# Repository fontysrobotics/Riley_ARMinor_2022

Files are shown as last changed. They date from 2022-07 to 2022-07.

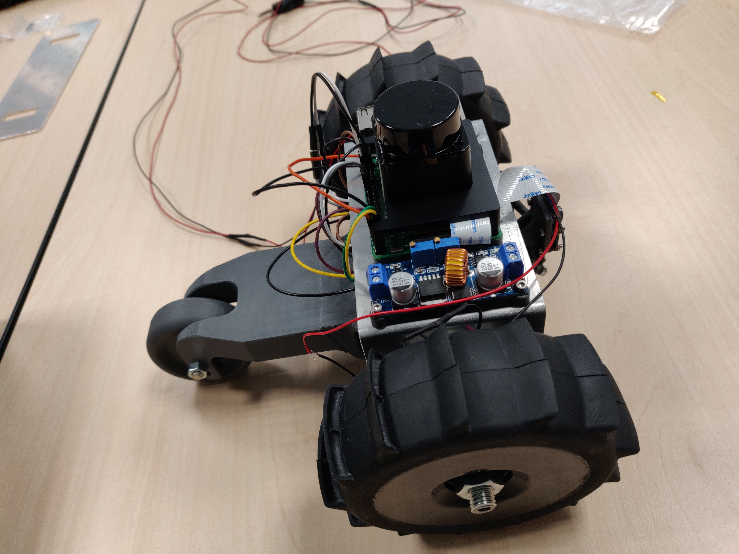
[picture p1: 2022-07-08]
docs/Environment_Preparations_RILey/pictures/Build-V0.1-Top.jpg

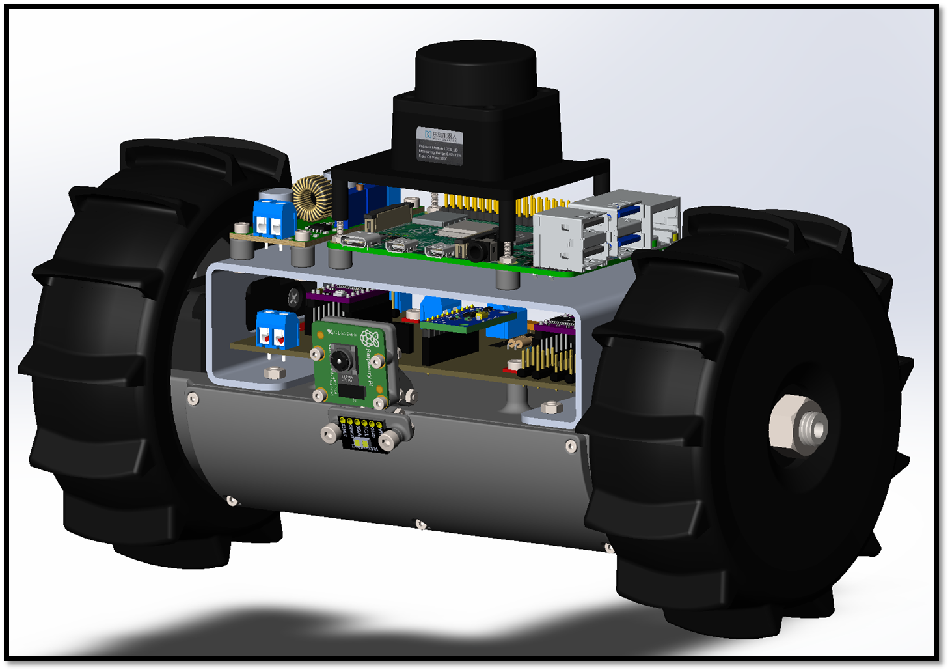
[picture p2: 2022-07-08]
docs/Environment_Preparations_RILey/pictures/LEGO_Assembly/Step17.png

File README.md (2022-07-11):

# Riley_ARMinor_2022
Remote indoor Inspection with Low-cost robots (RILey)
## Github file structure
- `docs` : in-development website containing documentation for the RILey robot, as well as pictures of the robot and meta information. Ideally could be run through Github Pages (can be setup in repository settings) but can also be built and run locally through VSCode.
- `documentation` : All documentation created during the project. This includes the initial project information, the plan of approach (before project requirements shifted drastically), datasheets for some of the components, the technical documentation for setting up many aspects of the robot and server systems, plus additional video material.
- `electrical` : Documentation related to the electrical design of the RILey robot, including version 1 and 2 of the PCB design, notes regarding problems encountered in the PCB design and explanations/schematics for the global electrical connections.
- `ros2` : Code files needed to run the robot (physical and simulation) through ROS2-foxy. More info included in technical document. Included are:
  - `riley_ws` : Main ROS workspace containing all the packages and launch files for both robot and server side.
  - `simulation` : ROS workspace used for simulating the robot in a virtual environment (Gazebo).
  - `yolov5` : Separate directory used to store the YOLOv5 object recognition model.
- `solidworks` : Solidworks CAD files making up version 1 and 2 of the RILey robot, including imported assets. Additional folders for STL/DXF component exports also available, though not needed for the CAD assemblies.

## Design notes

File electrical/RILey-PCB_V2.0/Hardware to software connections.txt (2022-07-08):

Physical pin:	GPIO pin:	Connection:
01:			None	:	3V3,	used by TOF
02:			None	:	5V,	used to power the Raspberry Pi 4b
03:			2	:	SDA,	used for I2C to sensors
04:			None	:	5V,	used to power the Raspberry Pi 4b
05:			3	:	SCL,	used for I2C to sensors
06:			None	:	GND,	used for power
07:			4	:	NC,	spare available at front pins labeled 14
08:			14	:	TX,	spare available at front pins labeled 15	
09:			None	:	GND,	used for power	
10:			15	:	RX,	used for receiving lidar information	
11:			17	:	lidar 'pwm' pin, used for rotation speed
12:			18	:	lidar enable pin, used to turn on the lidar
13:			27	:	NC,	spare available at front pins labeled 13
14:			None	:	GND,	used for power
15:			22	:	stepper motor mode0
16:			23	:	stepper motor mode1
17:			None	:	3V3,	used by TOF
18:			24	:	stepper motor mode2
19:			10	:	NC,	spare available at front pins labeled 12
20:			None	:	GND,	used for power
21:			9	:	NC,	spare available at front pins labeled 11
22:			25	:	NC,	spare available at front pins labeled 10
23:			11	:	NC,	spare available at front pins labeled 9
24:			8	:	NC,	spare available at front pins labeled 8
25:			None	:	GND,	used for power
26:			7	:	NC,	spare available at front pins labeled 7
27:			0	:	NC,	spare available at front pins labeled 6
28:			1	:	NC,	spare available at front pins labeled 5
29:			5	:	stepper motors disable
30:			None	:	GND,	used for power
31:			6	:	stepper motor 1 direction
32:			12	:	stepper motor 1 step
33:			13	:	stepper motor 2 step
34:			None	:	GND,	used for power
35:			19	:	NC,	spare available at front pins labeled 4
36:			16	:	NC,	spare available at front pins labeled 3
37:			26	:	stepper motor 2 direction
38:			20	:	NC,	spare available at front pins labeled 2
39:			None	:	GND,	used for power
40:			21	:	NC,	spare available at front pins labeled 1

Legend:
3V3:	3.3 Volt
5V:	5 Volt
SDA:	one of the I2C lines
SCL:	one of the I2C lines
GND:	ground
NC:	Not Connected / not used / available
TX:	uart transmit
RX:	uart receive

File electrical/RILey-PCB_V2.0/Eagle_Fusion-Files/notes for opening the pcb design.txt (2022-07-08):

If you want to open the "RILey-PCB_V2.0_v99.f3z" file, you have to open fusion (360) and make a workspace, and upload this file.
Then it downloads all the files that have been made before.

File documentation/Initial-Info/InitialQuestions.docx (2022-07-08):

1. Main use cases with examples. What should be prioritized?
- As many as possible, priority is our choice
- Collapsed area, eventually finding humans. (search and rescue)
2. Are CAD files and software files available for the prototype and completed robot?
- Company question.
3. Hardware datasheet with specifications for the sensors, robot manual and other documentation?
- Should be.
4. Does it need to go outdoors?
- No
5. Does it need to climb ramps or do other non-2D movements?
- No 3D needed.
6. Can we adjust existing parts of the robot or only add new ones?
- If needed you can add, if justified. (modifying not sure yet)
7. What’s the budget? Define Low-cost.
- Below €10k, currently the robot is €3k.
- Everything is discussed with Sjriek. (€1k generic)
8. Upside down movement, is it possible/defined as a use case?
- Not a question, NO.
9. What should be inspected/detected (things)?
- As many as possible, at least 3 (must), up to 10 (should), more (could)
10. When do we get the physical robot?
11. What comm protocol does the robot use to communicate with the server?
- Wifi for now, other as a should
12. What should be the server specifications?
- For now your laptop.
13. Should manual override still be available?
- Yes
14. What kind of alerts should the robot send to operators?
- Company question
15. Are we allowed to modify the given physical robot?
- Look above
16. Should the robot try to “save itself”? I.e., return to exit in case of low battery.
- YES

Multiple robots working together: Must? (should) (cool, really nice)

Other ideas:

- Add LiDAR (think 360 vs fixed FoV, Flash vs line scan)

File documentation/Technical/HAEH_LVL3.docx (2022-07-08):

Adaptive Robotics minor

Hardware Abstraction & Embedded Systems

28-6-2022

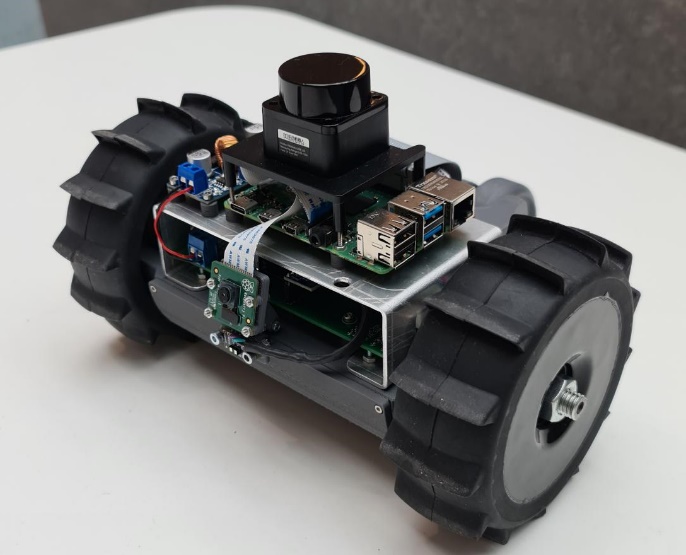
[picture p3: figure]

Name: Student number:

Toby van Dueren den Hollander 3679438

Quinvey Etienne 3566293

# Introduction

The Riley is a collaboration project between TMC and Fontys. TMC has approached Fontys with the goal of making their robot platform smarter with the use of additional sensor and logic. These improvements should make it possible to do autonomous reconnaissance of a building.

Because of IP related problems the platform itself could not be obtained from TMC. Therefore a mockup of the platform was made during the first months of the project. The dimensions and general shape of the mockup was modeled in a way to represent the original robot as accurate as possible.

In order to aid human and autonomous operations a few extra functions have to be added to improve control of the RILey robot platform.

# Problem Definition

During operation of the platform a few problems came up regarding movement and perception of the robot in its environment.

### Flipping

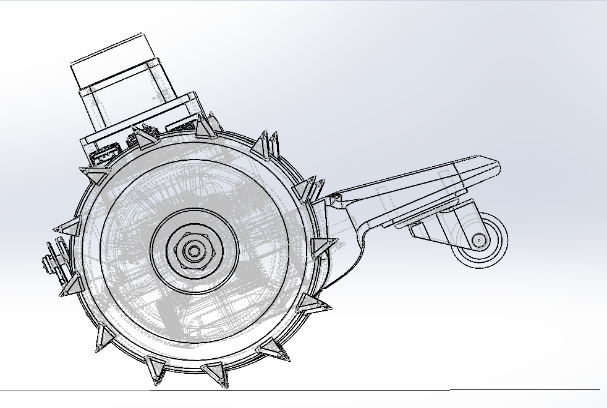
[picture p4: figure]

The first problem regards accelerating in backwards direction. The robot was initially designed to only drive forward. Accelerating backwards too quickly will result in a rotation flipping the robot as seen in the image below.

ω_rot

A_accel

Figure 1 Robot rotating

### colliding

Secondly, the lidar is able to visualize the surrounding of the robot. However, when objects are below the height of the lidar, the robot will not be able to detect the obstruction. This results in the robot bumping into smaller objects as seen below.

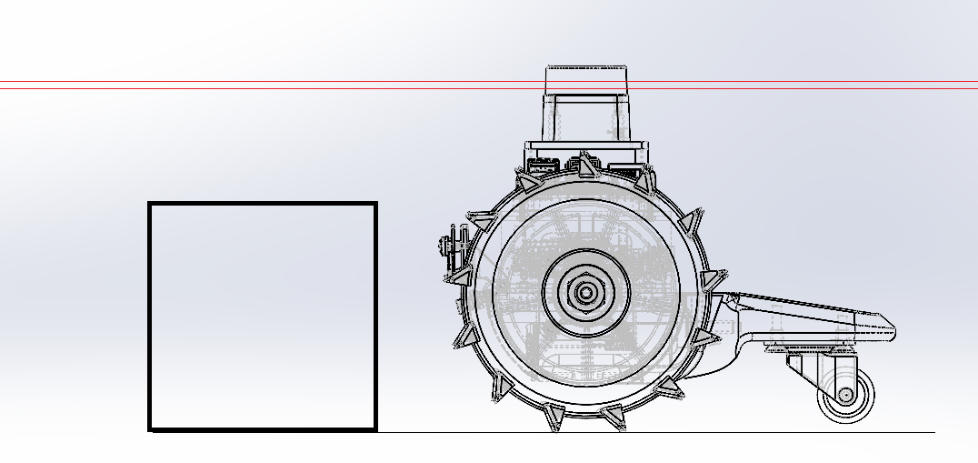
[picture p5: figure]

Figure 2 Robot just before hitting object

### Falling

Lastly the robot is not able to detect the presence of gaps, holes or other height differences in terrain. This can result in the robot falling of surfaces such as stairs.

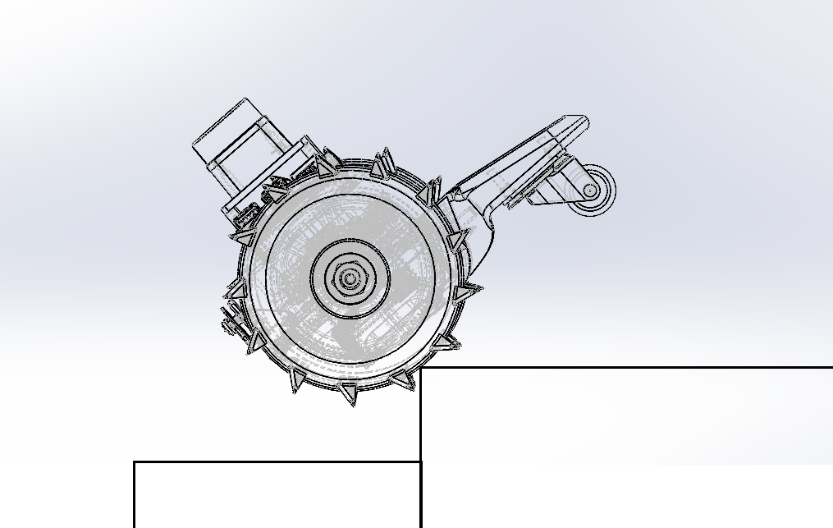
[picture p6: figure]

Figure 3 Robot falling of edge

# Solution of the problems

To provide a solution for the problems described above additional sensors are added to the robot. These include the MPU9250 and the VL53L1X. The MPU9250 contains a 3 axis gyroscope. This gyroscope can sense changes in the angular orientation of the robot. This can help preventing the robot from flipping. The VL53L1X Time of Flight sensor can measure distance by using infrared light. This sensor was used to prevent the robot hitting objects or driving into gaps.

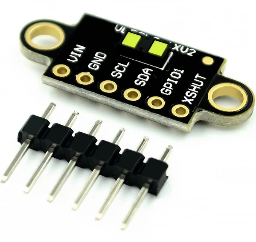
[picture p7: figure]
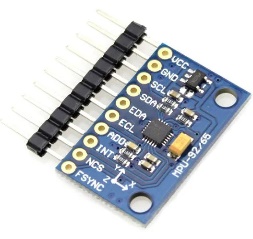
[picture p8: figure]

Figure 4 MPU9250 (left) and VL53L1X (right)

To prevent the robot from hitting a object the measured distance from the sensor cannot be less then a predefined threshold value. If this threshold value is reached, this means that there is a object on the robots track.

If the distance exceeds the threshold value corresponding to a gap value the robot will detect a gap.

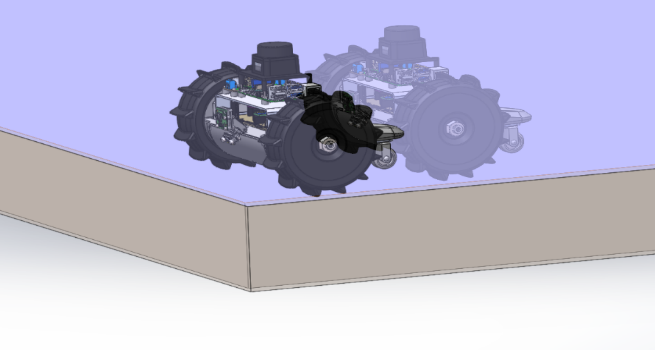
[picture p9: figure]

In both cases the robot should reverse so that it can easily turn away without hitting the object, or falling into the gap. The descision making is done on the raspberry pi itself. It overwrites input from both the user and/of the autonomous control.

Figure 5 Robot detecting gap

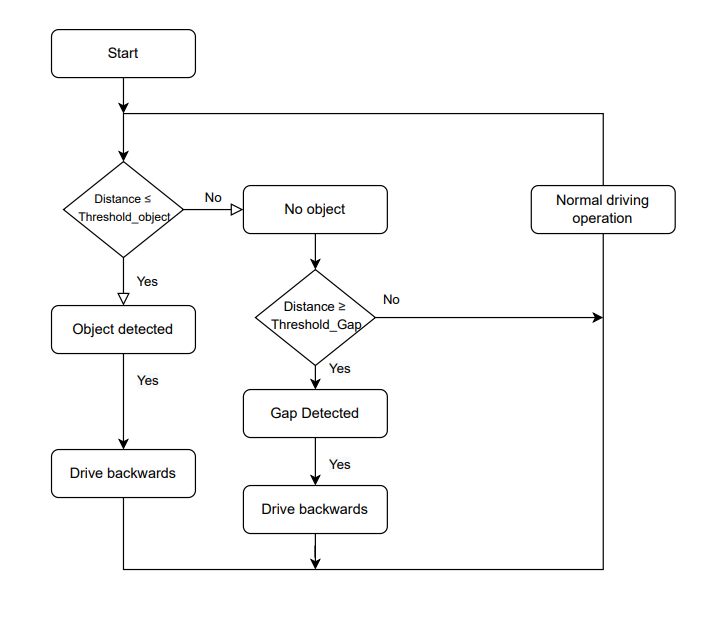
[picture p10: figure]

Figure 6 Logic illustrated in a flow chart

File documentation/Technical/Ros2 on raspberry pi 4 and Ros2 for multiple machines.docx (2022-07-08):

# Install ROS2 Foxy on Raspberry Pi 4

In this tutorial you will learn how to install ROS2 Foxy Fitzroy on Raspberry Pi 4.

ROS2 is a great framework/middleware for robotics applications. With a Raspberry Pi board you can go much further, and embed a complete ROS2 application inside a small robot.

For example, if you want to build a mobile base with wheels and a camera, well a Raspberry Pi 4 will be perfect for that. You can then create a network of robots all connected together.

## Which Raspberry Pi 4 version for ROS2 (RAM specs)

As you may know, the Raspberry Pi 4 board comes with different possible hardware configurations. You can choose between 2, 4 or even 8GB of RAM (previously also 1GB but discontinued).

If you currently have the 1GB version: 1 GB for Ubuntu Server + ROS2 is enough, but you’ll probably be limited in the future if you try to start more than a few nodes and launch files. If you want to avoid doing some optimization because of the RAM, I suggest you go with the 2GB (or more) version of the board.

After 2GB, then it’s quite simple: more RAM means more expensive. For starting and prototyping with ROS2, 2GB should be enough.

And one thing to keep in mind when using ROS2 on a Raspberry Pi: the Pi is certainly not as powerful as your computer/laptop, so you won’t be able to do 100% of what you do in your laptop, and some heavy features might run slower.

## Prerequisites: install Ubuntu Server 20.04

First you will need to install Ubuntu Server 20.04 on your Raspberry Pi 4 (https://roboticsbackend.com/install-ubuntu-on-raspberry-pi-without-monitor/).

We’ll use Ubuntu Server here because it’s probably the best suited OS for ROS2 on Raspberry Pi. ROS2 is really easy to install and works well on Ubuntu. For this tutorial you won’t need a desktop with Ubuntu on your Pi.

Also, as we’ll install ROS2 Foxy, make sure you have the version 20.04 for Ubuntu, since each version of ROS2 is only compatible with one Ubuntu version.

Once everything is setup and you have an Internet connection + ssh access to your Pi, you can start installing ROS2.

## Install ROS2 on Ubuntu on Raspberry Pi 4

Make sure to execute the commands in the order.

### Setup locale

sudo apt update && sudo apt install locales

sudo locale-gen en_US en_US.UTF-8

sudo update-locale LC_ALL=en_US.UTF-8 LANG=en_US.UTF-8

export LANG=en_US.UTF-8

### Setup sources

sudo apt update && sudo apt install curl gnupg2 lsb-release

sudo curl -sSL https://raw.githubusercontent.com/ros/rosdistro/master/ros.key -o /usr/share/keyrings/ros-archive-keyring.gpg

echo "deb [arch=$(dpkg --print-architecture) signed-by=/usr/share/keyrings/ros-archive-keyring.gpg] http://packages.ros.org/ros2/ubuntu $(source /etc/os-release && echo $UBUNTU_CODENAME) main" | sudo tee /etc/apt/sources.list.d/ros2.list > /dev/null

### Install ROS2 core packages

Now that you have added the ROS2 repository to your sources list, update.

sudo apt update

And now you can install ROS2.

Important: here we won’t install ros-foxy-desktop, we’ll install ros-foxy-ros-base, which contains no GUI tools, just the bare minimum you need to write and execute your ROS2 programs.

sudo apt install ros-foxy-ros-base

The ros-foxy-ros-base package is in fact a collection of many other packages, so the list of stuff to install will be pretty big. This step may take a few minutes to complete.

### Install colcon (build tool)

After you’ll write some ROS2 code into your own packages, you’ll need to build those packages.

ROS2 uses colcon as a build tool (and ament as the build system). When you only install the ROS2 core packages, colcon is not here, so install it manually.

sudo apt install python3-colcon-common-extensions

### Auto-completion for ROS2 command line tools

ROS2 comes with a lot of useful command line tools, and if you want to be able to use auto-completion for those tools, you’ll need to install The argcomplete Python module. First make sure you have pip3 installed.

sudo apt install python3-pip

pip3 install argcomplete

## Setup your environment for ROS2

Great, ROS2 Foxy is now installed on your Raspberry Pi 4 with Ubuntu Server 20.04!

Now, in order to actually use ROS2, you’ll need to setup your environment every time you open a new session (terminal). To source your ROS2 installation in your environment, run

source /opt/ros/foxy/setup.bash

And because it won’t be that practical to do this for every new session you open, add this line to your bashrc.

echo "source /opt/ros/foxy/setup.bash" >> ~/.bashrc

So, from now on, every time you open a terminal, your bashrc will be executed and your environment will be ready for ROS2.

## A few tips on how to best use ROS2 on Raspberry Pi

As you saw during the installation, we didn’t install any GUI tool, just the minimum to get things running.

If you need to use some visualization tools, such as Rviz or Gazebo, or if you need to do some heavy processing, then you might use a multi-machine setup with your Pi (or multiple Pis) and a more powerful computer/laptop. It’s very easy to make multiple machines communicate between each other with ROS2. You can run the programs that control hardware on your Raspberry Pi, and then exchange data – through ROS2 communication features – with your laptop, which will handle any GUI or heavy processing tasks.

Also, as you’ve only installed the core base, you might sometimes have to install additional packages.

To install a new ROS2 package, it’s quite easy: the name of the package will be “ros-distribution-package-name”. So if you want to install, on ROS2 Foxy, the example-interfaces package (which contains message and service definitions you can use when you get started with ROS2), you will run

sudo apt install ros-foxy-example-interfaces

# ROS2 Multiple Machines Tutorial (including Raspberry Pi)

In this tutorial you will learn how to run ROS2 on multiple machines, including a Raspberry Pi 4 board. As you’ll see, things will be quite easy and there is almost no configuration to do.

If you’re using a Raspberry Pi with ROS2 as one of the machines, make sure you have correctly installed ROS2 on your Pi (https://roboticsbackend.com/install-ros2-on-raspberry-pi/). Then, as you’ll see, no extra setup is required.

For this tutorial I will personally use a laptop running Ubuntu on a virtual machine (with a bridged adapter), and a Raspberry Pi with ROS2 on Ubuntu Server.

## Network configuration for ROS2 multi-machines

Before starting, obviously make sure you have installed ROS2 on each machine, preferably the same distribution.

Then, make sure you don’t have a firewall blocking your communications on the network. If you have a firewall, allow UDP multicasting, or disable the firewall at least during your first tests.

Connect all your machines in the same network. This is very important, otherwise they simply won’t be able to find each other.

Now, you can easily check if the machines can reach out to each other.

First, get the IP address of each machine inside the network by running

hostname -I

Example:

- Machine 1:
- hostname -I
- returns 192.168.43.138 172.17.0.1
- Machine 2:
- hostname -I
- returns 192.168.43.56

You may have multiple IP addresses on each machine, depending on what you’ve previously configured (ex: on Machine 1 I have Docker, this is why you see 172.17.0.1). Just find the IP addresses that are on the same network, here those who start with 192.168.43.xx.

If you can ping the machines from each other then the network configuration is done.

Machine 1:

$ ping 192.168.43.56

PING 192.168.43.56 (192.168.43.56) 56(84) bytes of data.

64 bytes from 192.168.43.56: icmp_seq=1 ttl=64 time=128 ms

64 bytes from 192.168.43.56: icmp_seq=2 ttl=64 time=136 ms

^C

Machine 2:

$ ping 192.168.43.138

PING 192.168.43.138 (192.168.43.138) 56(84) bytes of data.

64 bytes from 192.168.43.138: icmp_seq=1 ttl=64 time=8.75 ms

64 bytes from 192.168.43.138: icmp_seq=2 ttl=64 time=132 ms

^C

## Run ROS2 on 2 machines

Now it’s very simple. All you have to do is to start some nodes in Machine 1, some other nodes in Machine 2, and they will all be able to communicate through topics, services and actions. Just like they were all in the same machine.

Machine 1:

$ source /opt/ros/your_ros2_distribution/setup.bash # You can put that line into your ~/.bashrc

$ ros2 run demo_nodes_cpp talker

Machine 2:

$ source /opt/ros/your_ros2_distribution/setup.bash # You can put that line into your ~/.bashrc

$ ros2 run demo_nodes_cpp listener

And you should see logs on both machines!

If you want to communicate with a third/fourth/… machine, simply follow the network configuration steps again, and you’ll be all set.

## Use ROS_DOMAIN_ID to run multiple (separate) ROS2 applications on the same network

So, after you’ve configured the machines to be in the same network, they are all part of the same ROS2 application. This can be a problem: what if you want to run 2 different ROS2 applications on the same network and on multiple machines? Here you might want to completely separate the applications from each other.

Well, that’s possible, you just need to set one environment variable before you start your nodes.

Before you start any node in one session (= one terminal), you need to export a new environment variable, named ROS_DOMAIN_ID, using a number for the value (preferably a low number, between 1 and 232). Then, only the nodes started in sessions with the same ROS_DOMAIN_ID will be able to communicate with each other.

Example:

Machine 1 – session (terminal) A:

$ export ROS_DOMAIN_ID=5

$ source /opt/ros/your_ros2_distribution/setup.bash

$ ros2 run demo_nodes_cpp talker

Machine 2 – session (terminal) B:

$ export ROS_DOMAIN_ID=5

$ source /opt/ros/your_ros2_distribution/setup.bash

$ ros2 run demo_nodes_cpp listener

Try to set a different ROS_DOMAIN_ID (or don’t set one at all) on Machine 2 – session B, and you’ll see that the communication won’t work.

Now, you can have any number of configuration:

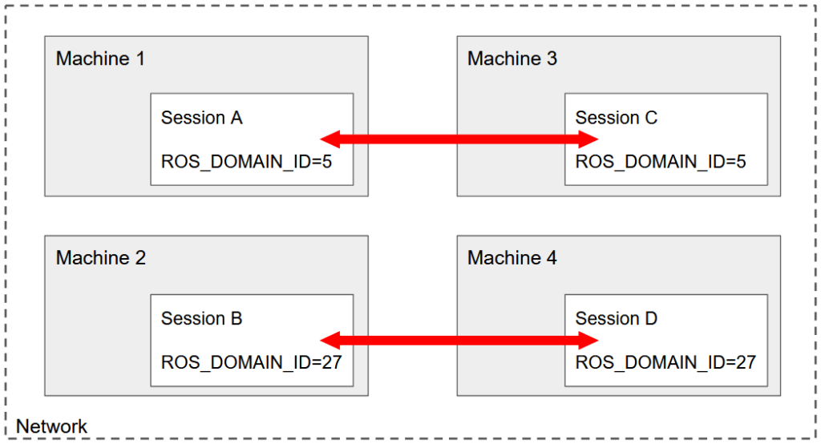
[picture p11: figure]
ROS2 Multiple Machines - Example with 4 Machines

Here you have 4 different machines, each starting one session. This is a classic example of what you can setup in real life.

In the future, make sure you don’t forget the ROS_DOMAIN_ID. If you know that all your sessions inside one machine will be used for the same application, you can add

export ROS_DOMAIN_ID=xx

to your ~/.bashrc.

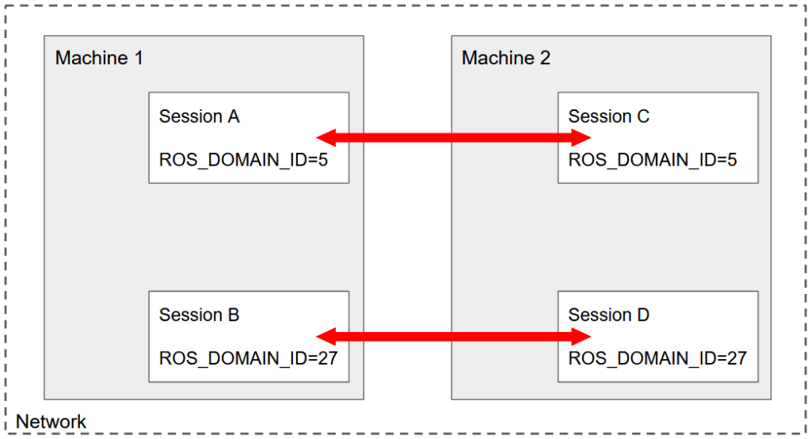
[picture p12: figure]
ROS2 Multiple Machines - Example with 2 Machines and 4 Sessions

But… You can also run multiple ROS2 applications on just 2 machines! What’s important is to understand that the ROS_DOMAIN_ID configuration is working at the session level, not the machine level – because it’s an environment variable.

## ROS2 multi-machine with Raspberry Pi

Running ROS2 across multiple machines is especially useful when you have a robot powered by a Raspberry Pi board, or any kind of embedded computer suitable for ROS2 (ex: Jetson Nano). Setting up your Pi for multi-machines communication is the same as setting up any other computer/laptop.

So, here is just an additional tip/best practice to keep in mind whenever you need to work with a robot powered by a Raspberry Pi.

If you want to make some experiments, or work with the robot simulation on the side, or do some heavy computing, etc., here is what you can do:

On your Raspberry Pi, just install the core packages, and run only the core nodes of your applications, which are responsible for talking to the hardware. Then, on your other (remote) computer, start any simulation tool such as RViz, Gazebo. Start your heavy nodes such as motion planning, etc.

This is a great way to minimize the CPU and RAM use on your Pi, and also to speed up your development time.

All in all, multiple machine communication is a really powerful ROS2 functionality. With ROS2 you can build a complete distributed system, not only on the software side, but also on the hardware side.

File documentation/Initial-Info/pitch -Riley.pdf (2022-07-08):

## Remote Inspection with Low-cost robots

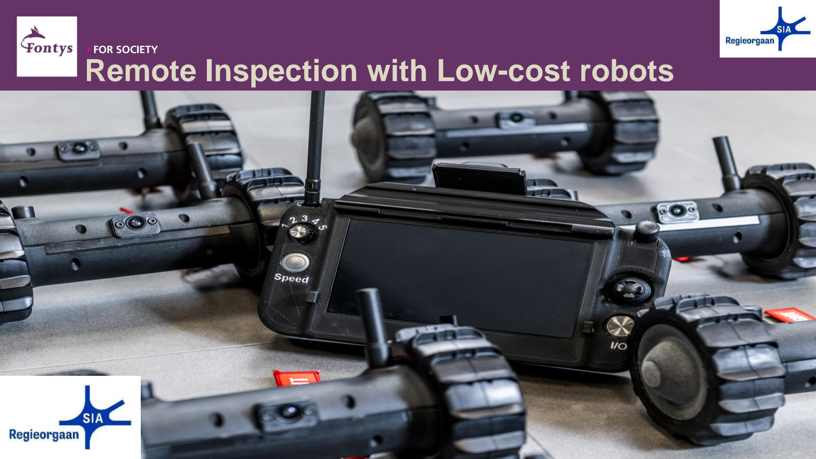
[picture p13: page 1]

- RILey is a project where we would like to accomplish technical challenges related to enable autonomous inspection for low cost robots in indoor our outdoor environments.
- In this project we would like to implement, improve and validate autonomous remote control of the SITA robot, that is provided by SITA Robotics, TMC and Avular are technology partners in this project. The project is funded by SIA.

# General Project Focus

Can we use the existing low-cost SITA robot, which is intended for remote-controlled reconnaissance, for autonomous inspection without substantially modifying

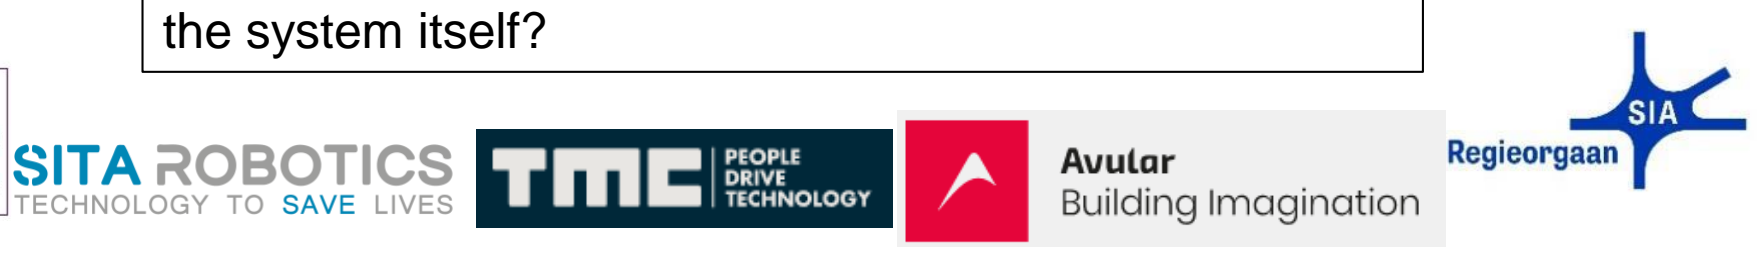
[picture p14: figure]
the system itself?

# Impression SITA robot

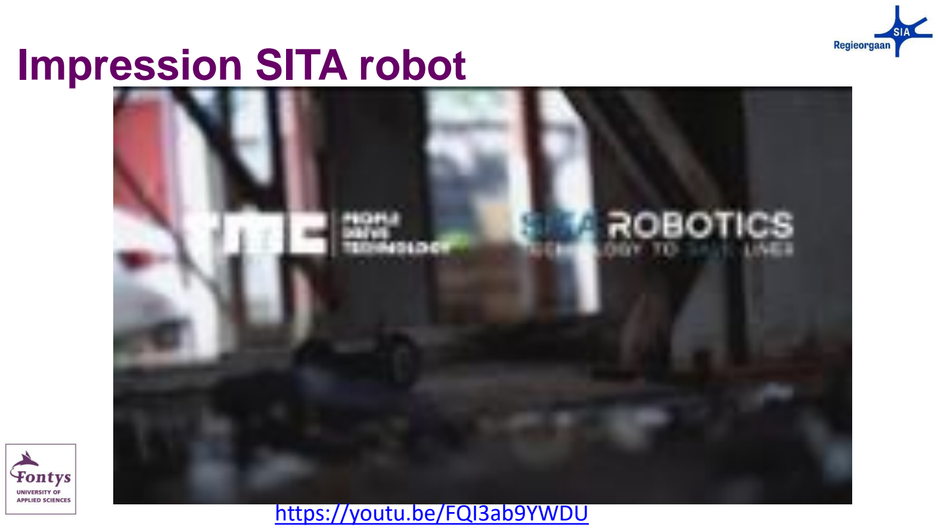
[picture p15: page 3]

https://youtu.be/FQI3ab9YWDU

## - How can you efficiently and autonomously scan a building using (multiple) remote controlled robots

# Main focus for you

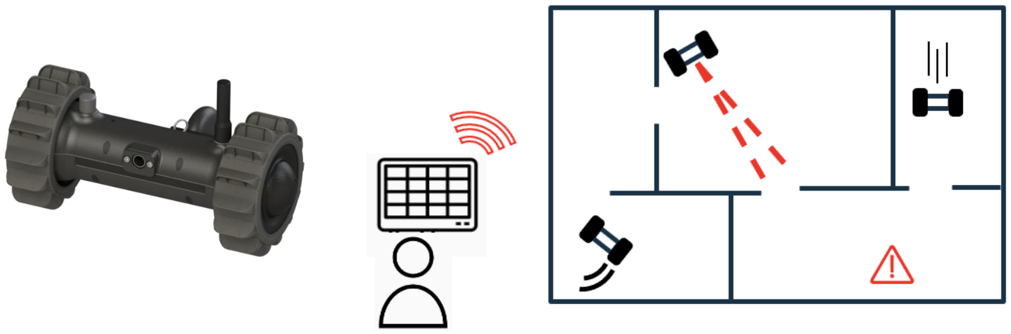
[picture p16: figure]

- Sketch scenarios
- Analyze the current status of the hardware and investigate the provided / needed technologies and solution.
- Determine if the provided technology is sufficient to perform the given task. Investigate the need and contribution of adding (smart) sensors, E.g., the use of a smart camera system (e.g. openmv-h7) or a small lidar could be beneficial for the project
- Investigate several methodologies that can be used for optimal area coverage to scan a building (e.g. there are biologically inspired techniques, or think of wall following techniques)

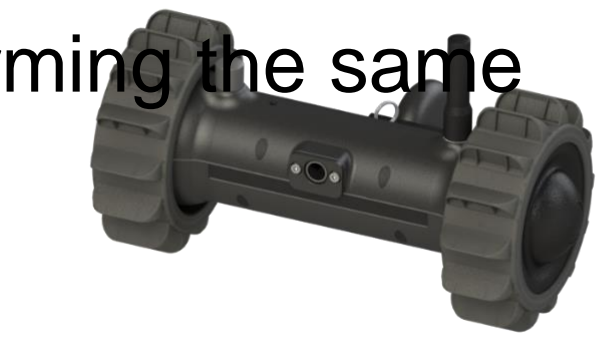
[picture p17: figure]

- Investigate how the system can benefit from multiple robots performing the same task at once

# Research

- Modify the system based on your requirements and research findings
- Create a digital counterpart of the real robot, for this you need to make the URDF / 3D model of the robot that can run in ROS/Gazebo.
- Integrate the additional sensors on the real robot as on the simulated model.
- Implement the model in simulation and validate if it behaves the same as the real robot in the same scenario.
- Test and validate the added sensors
- Implement and validate the chosen scenario of the use-case
- Implement and validate the chosen building scan methods (single vs multi robot)

# Design & Integration

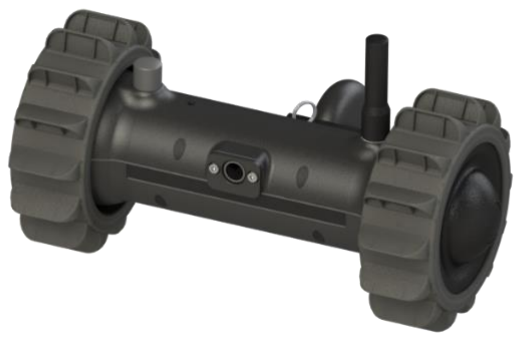
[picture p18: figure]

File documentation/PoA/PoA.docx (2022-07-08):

4-4-2022

Dueren den Hollander, Toby T. van, Etienne, Quinvey Q.S., Hinsberg, Niels N. van, Strolenberg, Martijn M.P.M., Păşescu, Alexandru A.R.

Fontys Adaptive Robotics

Remote Inspection with Low-cost robots

RILey

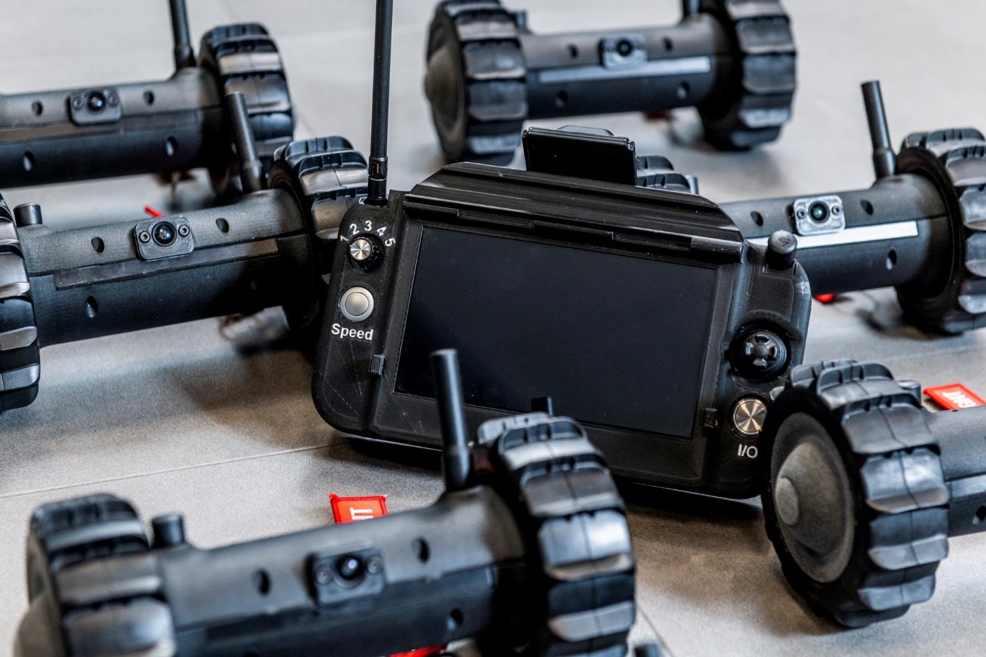
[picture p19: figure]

Fontys Adaptive Robotics Minor.

Engineering

Starting date: 04 April 2022 voice reading

End date: 08 July 2022

Presentation date: 06 July 2022

Student information:
Name | Alexandru Păşescu | Martijn Strolenberg | Niels van Hinsberg | Quinvey Etienne | Toby van Dueren den Hollander
Student number | 3806405 | 3638928 | 3958477 | 3566293 | 3679438
Profile | ICT & Technology | Mechatronics | Mechatronics | Electrical Engineering | Mechatronics

Project information:
Name of project | RILey minor project
Department | Fontys Adaptive Robotics Minor
Address | de Rondom 1, 5612 AP Eindhoven

Stakeholder information:
Name | Sjriek Alers, Pablo Negrete
Role | Client
Company | Sita Robotics, TMC, Avular, SIA, Fontys

Mentor information:
Name | Albert Aslan

Document information:
Title | Plan of Approach
Revision | V2.0
Date | 20 April 2022

Table 1: General information

# 1. Introduction

The main purpose of this project is to investigate whether a low-cost robot, which is intended to be controlled remotely, can be adapted to perform autonomous multi robot environmental inspection. A small and cheap robot is extremely suitable for this application. It could be used anywhere and could easily be taken with you. With affordable robots, it would also be possible with multiple robots to scan a large location faster. The partnership for this project consists of several stakeholders: SITA Robotics which is a company that wants to put its product on the market, TMC and Avular that are 2 technology partners and finally Fontys that is a research partner that needs to come up with innovative solutions.

# 2. Project Definition

## 2.1 Problem Definition

The main question of this project is to determine whether a low-cost robot, which is intended to be controlled remotely, can be adapted to perform an autonomous multi robot environmental inspection. With affordable robots, it should also be possible with multiple robots to scan a large location faster. One of the challenges is that the existing low-cost robot does not have the processing ability to perform the necessary sensor analysis and processing of the associated algorithms on the platform itself. Because of this, all sensor data from the robot needs to be sent wirelessly to a server, this server will then do all the necessary data processing and uses the analyzed data to control the robot, so that it can take any actions on this. Therefore, the robot must have the least number of sensors, but still be able to do the job accurately enough to be useful for the server. A mockup robot must be made to verify the simulations. The problem comes down to making multiple robots autonomously search for specified objects by working together.

## 2.2 Project Goals

The project can be defined in goals as well. The main goal is to create a system capable of commanding and communicating with the swarm of robot platforms. This system should be able to combine the sensory information it receives into a comprehensive mapping solution that also highlights objects of interest which are detected by the robot swarm’s cameras. This requires research in multiple subjects. The current state of the robot needs to be analyzed to understand what it’s capable of. Based on this a working mockup robot needs to be made. It may be necessary to add or even change out some of the sensors. In the section Time and Planning it is stated what kind of subgoals are needed to achieve the main goal.

## 2.3 User Requirements

The user requirements and their handling priority can be found in Table 2: User Requirements below.

No | User Requirements | MoSCoW
1 | Must go through the use case without getting stuck | Must
2.1 | Should detect at least 3 useful objects for example doors, windows, humans, walls etc. | Should
2.2 | Could detect 10 useful objects | Could
3.1 | The robot must not collide with static objects | Must
3.2 | The robot should not collide with moving objects | Should
4 | Multiple robots could map simultaneously in the same environment | Could
5 | Multiple robots should cover more ground in the same amount of time than 1 robot | Should
6 | The robot won’t need to go on stairs or ramps | Won’t
7 | Must be able to manually override the autonomous operations | Must
8 | The robot must return to starting point if it's below a certain battery level | Must
9 | Must model an URDF/3D model of the robot | Must
10 | Must simulate the robot model using Gazebo for validating the other requirements | Must
11 | Robot could create a map of its environment | Could
12 | Should use a limited set of sensors | Should
13 | Could add additional sensors/smart cameras | Could
14 | The robot must only act based on commands it receives | Must
15 | The battery could last at least an hour between charges | Could
16 | The budget used shouldn’t exceed €1000 | Should
17 | The sensor-data must be processed server-side | Must
18 | Must make a simple mock-up robot | Must

Table 2: User Requirements

## 2.4 Project Boundaries

The project will be primarily seen as failed if the end result doesn’t consist of all (must) requirements. In addition, other (unexpected) situations may arise. For example, if the product ultimately turns out not to be profitable or the client isn’t satisfied with the result, this will cause many unexpected/unnecessary costs.

# 3. Phasing

The V-model will be used to measure progress for this project. There are different phases of the project that are chronologically executed. Also, testing is a part of each phase so that nothing will be overlooked.

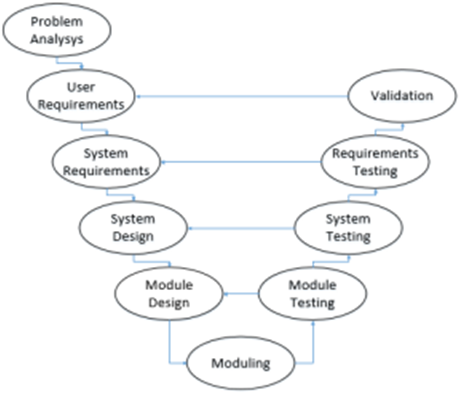
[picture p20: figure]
wfd

## 3.1 Problem Analysis

Figure 1: V-model

The existing low-cost robot does not have sensors to navigate in its environment, nor does it have the capability to perform the necessary sensor analysis and processing of the associated
algorithms on the platform itself. Some sensors need to be integrated to allow the robot to navigate autonomously. Additionally, all sensor data from the robot should be sent wirelessly to a server. This server will then perform the necessary data processing and send its guidance back to the robot, so that it can change its movement accordingly.

An additional challenge will be how the robot can locate itself with a limited set of sensors in an (un)known environment. This localization will also have to be carried out remotely.

## 3.2 User Requirements

The client plays a major role in defining the user requirements. There will be a set of questions made regarding the RILey robot that the client needs to answer so that user requirements can be fully defined. In this phase it is very important to ask good questions and get the best answers because this will be the foundation of the whole project.

## 3.3 System Requirements

In this phase of the project the user requirements will need to be translated into technical system requirements. The main research subjects will be:

1) Will the already integrated sensors be useful for navigation and object detection?

2) Which sensors are sufficient to get enough information to execute the SLAM algorithm reliably?

3) Which camera specifications are needed to detect the wanted objects?

4) How will the communication protocol look like (what does the robot process and what does the server process)?

5) How will the robot autonomously navigate and map with SLAM an unknown building location from the inside?

6) How will the robot detect moving objects?

7) Is using more RILey robots beneficial for reaching the end goal faster?

## 3.4 System Design

The current RILey robot needs to be modified to fulfil the needs of the user requirements laid above. This means additional hardware needs to be integrated therefore the mechanical construction needs to be changed. The electrical system needs to be modified to supply every module power and this will influence the battery life. Every module also needs to communicate correctly with the controller or server so a communication architecture should be made.

## 3.5 Module Design

In this phase the different software modules are going to be designed. There needs to be an algorithm which covers the movements of the RILey robot in order to make a map of the environment. The robot should detect moving objects when it's in surveillance mode, therefore an algorithm needs to be designed to find the difference in static object and moving objects. Also there needs to be some reliable object recognition with vision technology. The robot must know the type of object it sees and how certain it is that it is the actual object and not some different object. After that there needs to be defined what the computer in the robot is going to process and what the server is processing. The goal is that the actual robot will do as little processing as possible, the robot will only control the motors and send information like camera feed over Wi-Fi to the server. The server then has all the smart algorithm computing like SLAM and object detection. At last, there needs to be a module designed that can control multiple robots to speed up the process of mapping a building or locating objects.

## 3.6 Implementation

When everything is defined and designed the actual implementation begins. Here the robot gets physically be built with its modifications. There will be some mechanical work probably 3D printing for concept because it is fast and easy. The electrical connection needs to be made reliable and as clean as possible so no cables will be sticking out. Then the software code needs to be uploaded to the robot(s) and set up the server so the two of them can communicate.

## 3.7 Module Testing

In the module testing phase the designed modules are being tested on their functionality. The movement algorithm for mapping an environment will be tested in a simulation program called Gazebo. If it's possible it will be also tested on the real RILey robot in the physical world. When the movement algorithm is being tested it simultaneously tests the SLAM algorithm with making a map of the explored space. The vision detection algorithm can be tested with graphically printing the information what the robot thinks the object it is looking at.

## 3.8 System Testing

The different modules also need to work together to make the system work. In order to test this, a use case scenario is created where the robot needs to map the location and detect a certain object after that, the initially detected object will move to a different location, and it needs to log where the object new location is at. Additionally, this process can be sped up by testing multiple RILey robots in the same environment mapping the location together and scanning objects.

## 3.9 Requirements Testing

If the system testing is successfully finished it is important to validate if the user requirements are met. At least the “must” requirements need to be fully integrated. After that the focus will be on the should and could requirements. Because this is a large project it is not expected to fulfil all user requirements in the given timeframe.

## 3.10 Validation

in this phase it will be interesting how robust the system is behaving and if it will work in a different environment other than the use case. Eventually it is not a useful product if it can’t adapt to change. The end goal would be that it can navigate in any environment and can track as many objects as possible. In this phase there will be recommendations written for other developers to build off from.

# 4. Project Control

## 4.1 Organization

The project will be organized using a parallel waterfall model, where the group may be divided into sub-groups, each overseeing one or more modules in the project at any given time. The waterfall model is favored over a SCRUM approach largely due to the nature of the project. In this case, many of the goals and requirements depend on previously achieved steps, and there are planning limitations stemming from the hardware dependency and real-life scenario tests that are needed to validate the system.

The group will not have a de-facto project leader, given the divide-and-conquer strategy described above, however within each sub-group there may be individualized leadership and strategizing. Overall, the team will hold daily meetings in which the status of each sub-group of people will be explained and inter-modular planning will occur based on results. At the same time, one person will be assigned to the role of main team communicator. They will communicate with the clients about the project developments.

## 4.2 Time and Planning

Milestones:

1) Contact the company and receive the robot and documentation

2) Define user requirements

3) Successfully create the robot simulation environment

4) Mapping an environment and transmit it to the server

5) Object recognition and localization by 1 robot

6) Communicate with multiple robots

7) Merging the mapping, and object recognition localization with multiple robots.

8) Delivery of final products and report

# 5. Risks

There are always project risks during the duration of the project. Not all these risks can be avoided. Identifying risks in time can negate much of the negative consequences of the risk. Achieving this requires that potential risk is known, and how to combat the consequences of each of them.

## 5.1 Project Risks

Not all risk can be identified or are worth mentioning. Therefore, some common risks are mentioned.

- Not enough time. Due to the lack of time, one or more requirements cannot be met.

- No clear project objective. The objective should be crystal clear to every member of the group. This is needed to work towards the same goals.

- Communication problems. Communication is key in group projects. Improper communication can lead to delays in the project

- Incomplete project planning. An incomplete planning can lead to more work required that predicted in the beginning.

- Absence of project members.

- Absence of project tutor.

- insufficient support external companies

- COVID-19 Lockdowns

- Delayed arrival of goods

- Poor performance of group member(s)

## 5.2 Risk Classification

Classifying risk is done using the impact of the risk when things go wrong, and the chance this events occurs. The impact is measured in the amount of time lost, because time is one of the most important resources during projects. The multiplication of these two factors determines the risk degree. Besides the risk degree the risk priority is useful the know. This can be quantified by multiplying the risk impact with the vulnerability you have for the risk. This can be summarized in the following formulas:

Risk = Risk impact × Probability

Risk priority=Risk×Vulnerbility

Rating | Name | Progress loss
1 | Incidental | Less than a day
2 | Minor | One day to one week
3 | Medium | One to two weeks
4 | Major | Two weeks to a month
5 | Extreme | More than one month

Table 3: Impact scale

Rating | Name | Chance of occurrence during project
1 | Incidental | 0 – 10%
2 | Minor | 10 – 25%
3 | Medium | 25 – 50%
4 | Major | 50 – 75%
5 | Extreme | 75 – 100%

Table 4 Probability scale

Rating | Name | Description
1 | Incidental | Almost no impact on project result
2 | Minor | No severe impact on project result
3 | Medium | Project result at risk
4 | Major | Serious risk for project
5 | Extreme | Fatal risk for project

Table 5 Vulerability scale

Risk | I | P | V | Risk degree | Risk priority
Not enough time | 4 | 3 | 4 | 12 | 48
No clear project objective | 2 | 2 | 1 | 4 | 4
Communication problems | 1 | 1 | 2 | 1 | 2
Incomplete project planning | 2 | 2 | 1 | 4 | 4
Absence of project members | 3 | 1 | 2 | 3 | 6
Absence of project tutor. | 2 | 1 | 1 | 2 | 2
insufficient support external companies | 2 | 2 | 2 | 4 | 8
COVID-19 Lockdowns | 4 | 2 | 3 | 8 | 24
Delayed arrival of goods | 2 | 3 | 2 | 6 | 12
Poor performance of group member(s) | 2 | 1 | 2 | 2 | 4

Table 6: Classification of risks

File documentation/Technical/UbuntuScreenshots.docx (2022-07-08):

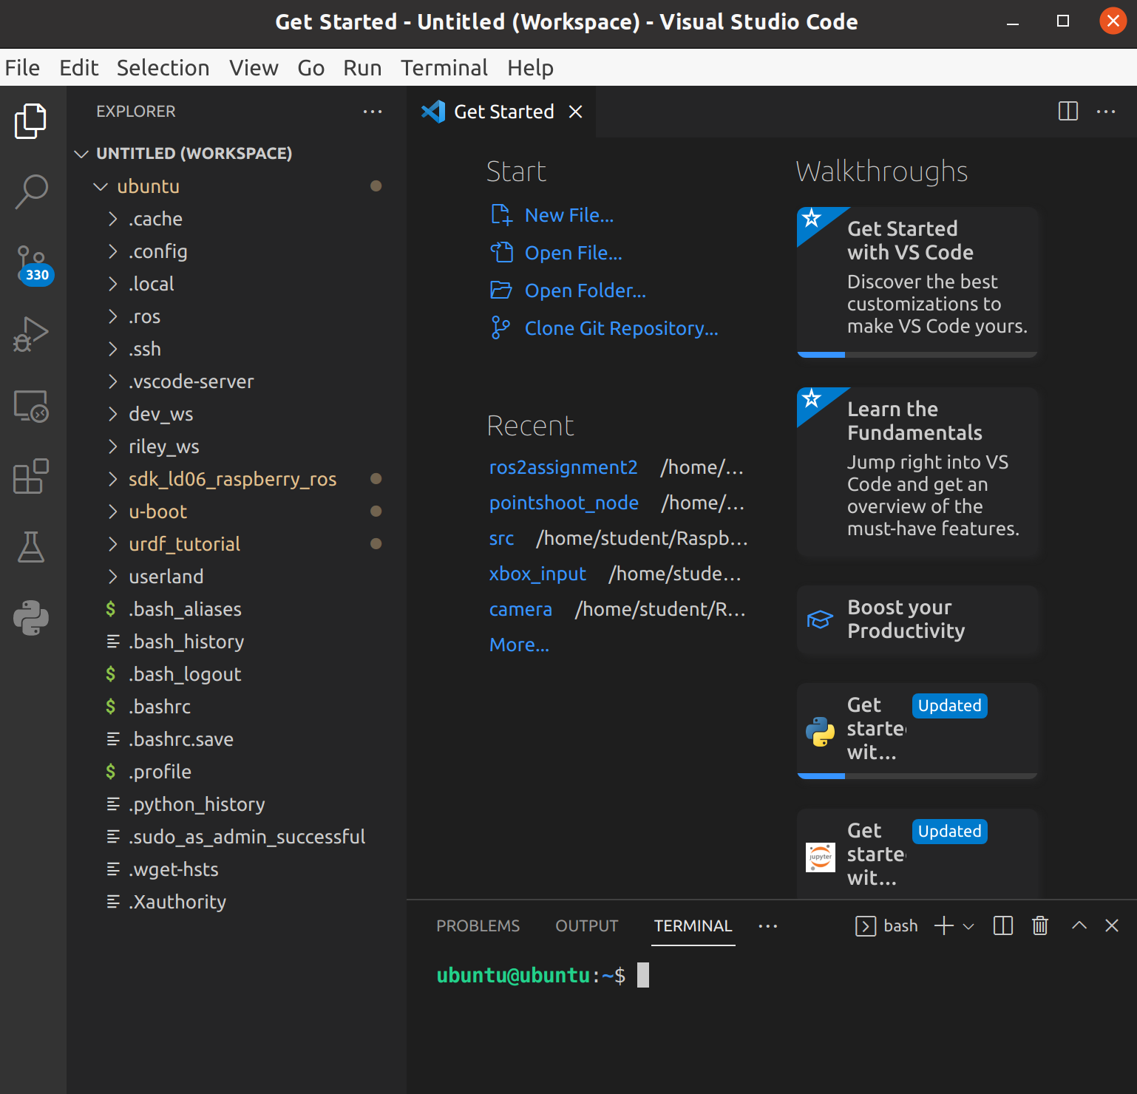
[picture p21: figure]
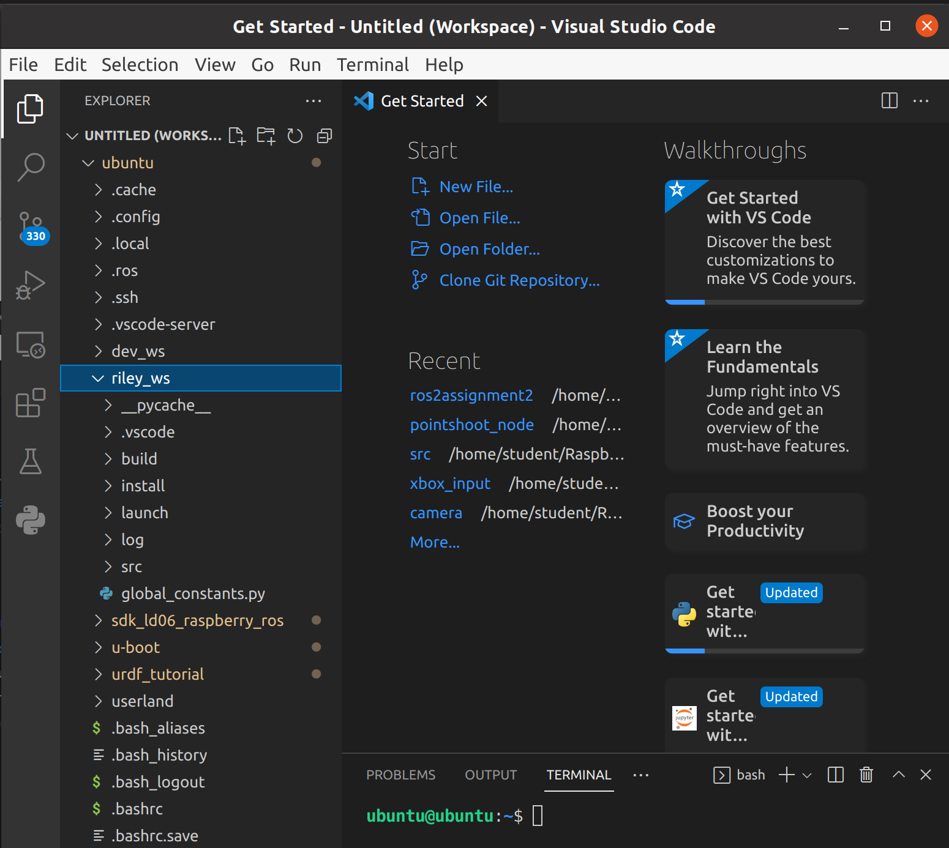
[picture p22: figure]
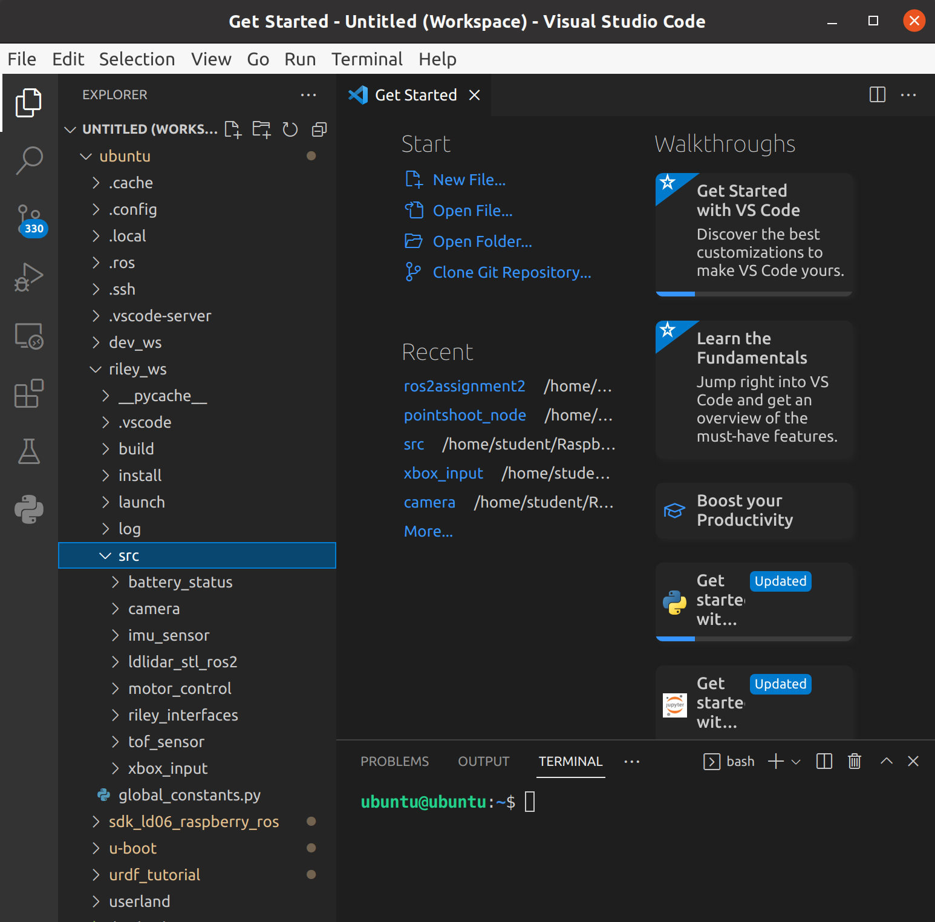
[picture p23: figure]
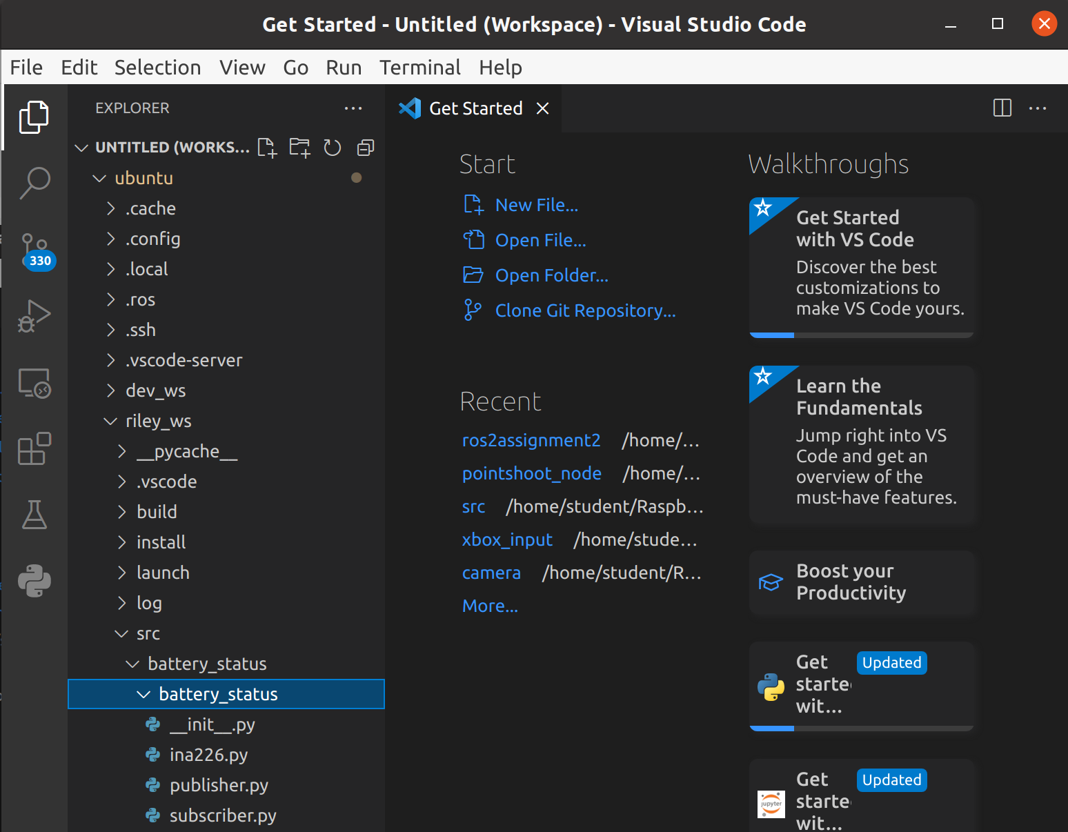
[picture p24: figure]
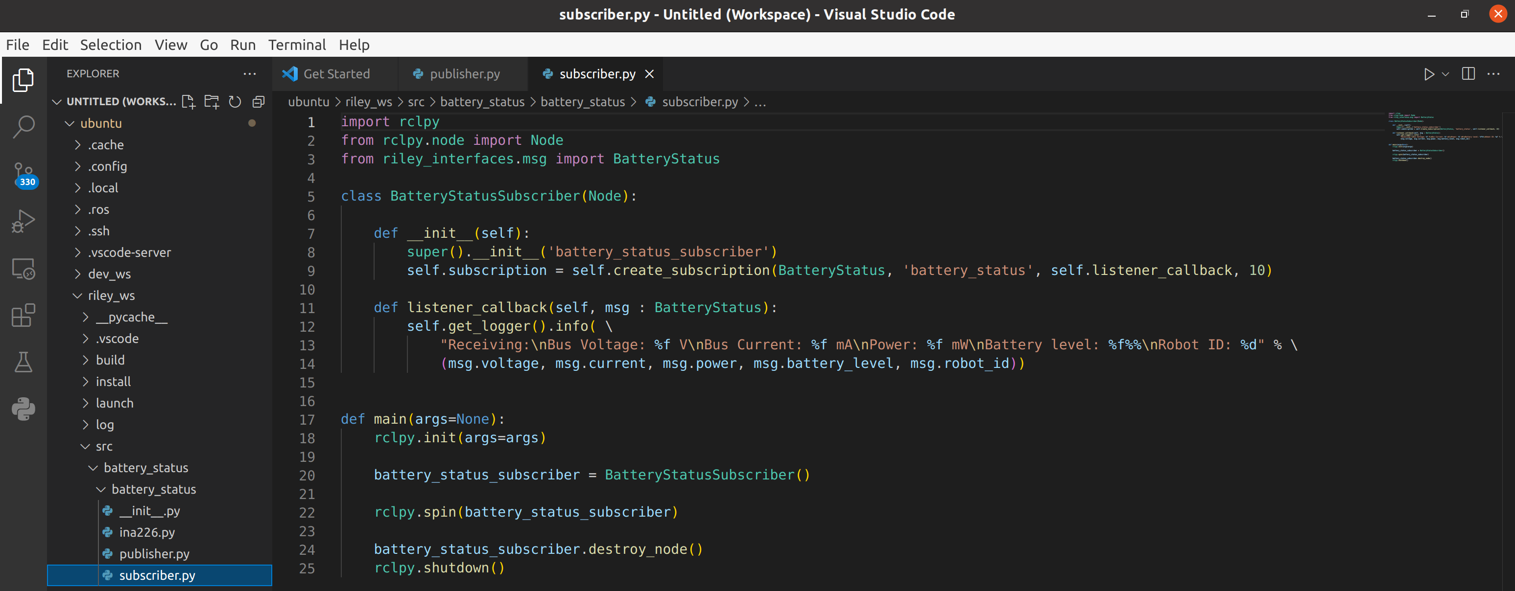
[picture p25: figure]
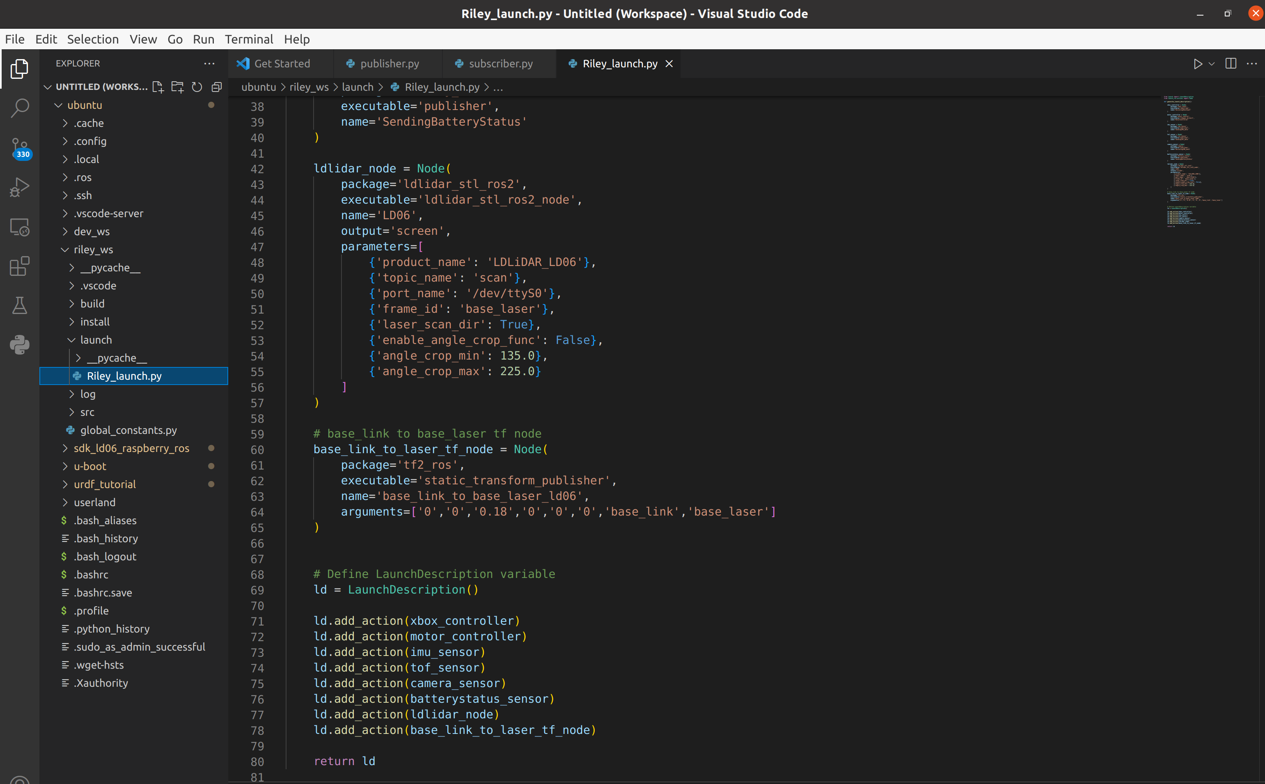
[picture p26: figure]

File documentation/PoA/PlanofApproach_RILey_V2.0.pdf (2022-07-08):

# 4-4-2022 Remote Inspection with Low-cost robots

RILey

Dueren den Hollander, Toby T. van, Etienne, Quinvey
Q.S., Hinsberg, Niels N. van, Strolenberg, Martijn
M.P.M., Păşescu, Alexandru A.R.
FONTYS ADAPTIVE ROBOTICS

## General Information

Fontys Adaptive Robotics Minor.

Engineering

Starting date: 04 April 2022 voice reading

End date: 08 July 2022

Presentation date: 06 July 2022

Student information:


Name | Alexandru Păşescu | Martijn Strolenberg | Niels van Hinsberg | Quinvey Etienne | Toby van Dueren den Hollander
Student number | 3806405 | 3638928 | 3958477 | 3566293 | 3679438
Profile | Technology ICT & | Mechatronics | Mechatronics | Electrical Engineering | Mechatronics

Project information:
Name of project | RILey minor project
Department | Fontys Adaptive Robotics Minor
Address | de Rondom 1, 5612 AP Eindhoven
Stakeholder information:
Name | Sjriek Alers, Pablo Negrete
Role | Client
Company | Sita Robotics, TMC, Avular, SIA, Fontys
Mentor information:
Name Albert Aslan
Document information:
Title | Plan of Approach
Revision | V2.0
Date | 20 April 2022
Table 1: General information

## Table of Contents

1. Introduction | 3
2. Project Definition | 3
2.1 | Problem Definition | 3
2.2 | Project Goals | 3
2.3 | User Requirements | 4
2.4 | Project Boundaries | 4
3. Phasing | 5
3.1 | Problem Analysis | 5
3.2 | User Requirements | 5
3.3 | System Requirements | 5
3.4 | System Design | 6
3.5 | Module Design | 6
3.6 | Implementation | 6
3.7 | Module Testing | 6
3.8 | System Testing | 6
3.9 | Requirements Testing | 7
3.10 | Validation | 7
4. Project Control | 8
4.1 | Organization | 8
4.2 | Time and Planning | 8
5. Risks | 9
5.1 | Project Risks | 9
5.2 | Risk Classification | 9

## List of Figures

Figure 1: V-model | 5 (https://stichtingfontys-my.sharepoint.com/personal/408293_student_fontys_nl/Documents/School/Minor/Adaptive%20Robotics%20Minor/MP6_Minor-Project/AR-MP6_RILey/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)

## List of Tables

Table 1: General information | 1
Table 2: User Requirements | 4
Table 3: Impact scale | 9
Table 4 Probability scale | 10
Table 5 Vulerability scale | 10
Table 6: Classification of risks | 10

## 1. Introduction

The main purpose of this project is to investigate whether a low-cost robot, which is intended to be controlled remotely, can be adapted to perform autonomous multi robot environmental inspection. A small and cheap robot is extremely suitable for this application. It could be used anywhere and could easily be taken with you. With affordable robots, it would also be possible with multiple robots to scan a large location faster. The partnership for this project consists of several stakeholders: SITA Robotics which is a company that wants to put its product on the market, TMC and Avular that are 2 technology partners and finally Fontys that is a research partner that needs to come up with innovative solutions.

## 2. Project Definition

### 2.1 Problem Definition

The main question of this project is to determine whether a low-cost robot, which is intended to be controlled remotely, can be adapted to perform an autonomous multi robot environmental inspection. With affordable robots, it should also be possible with multiple robots to scan a large location faster. One of the challenges is that the existing low-cost robot does not have the processing ability to perform the necessary sensor analysis and processing of the associated algorithms on the platform itself. Because of this, all sensor data from the robot needs to be sent wirelessly to a server, this server will then do all the necessary data processing and uses the analyzed data to control the robot, so that it can take any actions on this. Therefore, the robot must have the least number of sensors, but still be able to do the job accurately enough to be useful for the server. A mockup robot must be made to verify the simulations. The problem comes down to making multiple robots autonomously search for specified objects by working together.

### 2.2 Project Goals

The project can be defined in goals as well. The main goal is to create a system capable of commanding and communicating with the swarm of robot platforms. This system should be able to combine the sensory information it receives into a comprehensive mapping solution that also highlights objects of interest which are detected by the robot swarm’s cameras. This requires research in multiple subjects. The current state of the robot needs to be analyzed to understand what it’s capable of. Based on this a working mockup robot needs to be made. It may be necessary to add or even change out some of the sensors. In the section Time and Planning it is stated what kind of subgoals are needed to achieve the main goal.

### 2.3 User Requirements

The user requirements and their handling priority can be found in Table 2: User Requirements below.

No | User Requirements | MoSCoW
1 | Must go through the use case without getting stuck | Must
2.1 | Should detect at least 3 useful objects for example doors, windows, humans, walls etc. | Should
2.2 | Could detect 10 useful objects | Could
3.1 | The robot must not collide with static objects | Must
3.2 | The robot should not collide with moving objects | Should
4 | Multiple robots could map simultaneously in the same environment | Could
5 | Multiple robots should cover more ground in the same amount of time than 1 robot | Should
6 | The robot won’t need to go on stairs or ramps | Won’t
7 | Must be able to manually override the autonomous operations | Must
8 | The robot must return to starting point if it's below a certain battery level | Must
9 | Must model an URDF/3D model of the robot | Must
10 | Must simulate the robot model using Gazebo for validating the other requirements | Must
11 | Robot could create a map of its environment | Could
12 | Should use a limited set of sensors | Should
13 | Could add additional sensors/smart cameras | Could
14 | The robot must only act based on commands it receives | Must
15 | The battery could last at least an hour between charges | Could
16 | The budget used shouldn’t exceed €1000 | Should
17 | The sensor-data must be processed server-side | Must
18 | Must make a simple mock-up robot | Must
Table 2: User Requirements

### 2.4 Project Boundaries

The project will be primarily seen as failed if the end result doesn’t consist of all (must) requirements. In addition, other (unexpected) situations may arise. For example, if the product ultimately turns out not to be profitable or the client isn’t satisfied with the result, this will cause many unexpected/unnecessary costs.

## 3. Phasing

The V-model will be used to measure progress for this project. There are different phases of the project that are chronologically executed. Also, testing is a part of each phase so that nothing will be overlooked.


### 3.1 Problem Analysis

The existing low-cost robot does not have sensors to navigate in its environment, nor does it have the capability to perform the necessary sensor analysis and processing of the associated algorithms on the platform itself. Some sensors need to be integrated to allow the robot to navigate autonomously. Additionally, all sensor data from the robot should be sent wirelessly to a server. This server will then perform the necessary data processing and send its guidance back to the robot, so that it can change its movement accordingly.

An additional challenge will be how the robot can locate itself with a limited set of sensors in an (un)known environment. This localization will also have to be carried out remotely.

### 3.2 User Requirements

The client plays a major role in defining the user requirements. There will be a set of questions made regarding the RILey robot that the client needs to answer so that user requirements can be fully defined. In this phase it is very important to ask good questions and get the best answers because this will be the foundation of the whole project.

### 3.3 System Requirements

In this phase of the project the user requirements will need to be translated into technical system requirements. The main research subjects will be:

1) Will the already integrated sensors be useful for navigation and object detection?
2) Which sensors are sufficient to get enough information to execute the SLAM algorithm reliably?
3) Which camera specifications are needed to detect the wanted objects?
4) How will the communication protocol look like (what does the robot process and what does the server process)?
5) How will the robot autonomously navigate and map with SLAM an unknown building location from the inside?
6) How will the robot detect moving objects?
7) Is using more RILey robots beneficial for reaching the end goal faster?

Figure 1: V-model

### 3.4 System Design

The current RILey robot needs to be modified to fulfil the needs of the user requirements laid above. This means additional hardware needs to be integrated therefore the mechanical construction needs to be changed. The electrical system needs to be modified to supply every module power and this will influence the battery life. Every module also needs to communicate correctly with the controller or server so a communication architecture should be made.

### 3.5 Module Design

In this phase the different software modules are going to be designed. There needs to be an algorithm which covers the movements of the RILey robot in order to make a map of the environment. The robot should detect moving objects when it's in surveillance mode, therefore an algorithm needs to be designed to find the difference in static object and moving objects. Also there needs to be some reliable object recognition with vision technology. The robot must know the type of object it sees and how certain it is that it is the actual object and not some different object. After that there needs to be defined what the computer in the robot is going to process and what the server is processing. The goal is that the actual robot will do as little processing as possible, the robot will only control the motors and send information like camera feed over Wi-Fi to the server. The server then has all the smart algorithm computing like SLAM and object detection. At last, there needs to be a module designed that can control multiple robots to speed up the process of mapping a building or locating objects.

### 3.6 Implementation

When everything is defined and designed the actual implementation begins. Here the robot gets physically be built with its modifications. There will be some mechanical work probably 3D printing for concept because it is fast and easy. The electrical connection needs to be made reliable and as clean as possible so no cables will be sticking out. Then the software code needs to be uploaded to the robot(s) and set up the server so the two of them can communicate.

### 3.7 Module Testing

In the module testing phase the designed modules are being tested on their functionality. The movement algorithm for mapping an environment will be tested in a simulation program called Gazebo. If it's possible it will be also tested on the real RILey robot in the physical world. When the movement algorithm is being tested it simultaneously tests the SLAM algorithm with making a map of the explored space. The vision detection algorithm can be tested with graphically printing the information what the robot thinks the object it is looking at.

### 3.8 System Testing

The different modules also need to work together to make the system work. In order to test this, a use case scenario is created where the robot needs to map the location and detect a certain object after that, the initially detected object will move to a different location, and it needs to log where the object new location is at. Additionally, this process can be sped up by testing multiple RILey robots in the same environment mapping the location together and scanning objects.

### 3.9 Requirements Testing

If the system testing is successfully finished it is important to validate if the user requirements are met. At least the “must” requirements need to be fully integrated. After that the focus will be on the should and could requirements. Because this is a large project it is not expected to fulfil all user requirements in the given timeframe.

### 3.10 Validation

in this phase it will be interesting how robust the system is behaving and if it will work in a different environment other than the use case. Eventually it is not a useful product if it can’t adapt to change. The end goal would be that it can navigate in any environment and can track as many objects as possible. In this phase there will be recommendations written for other developers to build off from.

## 4. Project Control

### 4.1 Organization

The project will be organized using a parallel waterfall model, where the group may be divided into sub-groups, each overseeing one or more modules in the project at any given time. The waterfall model is favored over a SCRUM approach largely due to the nature of the project. In this case, many of the goals and requirements depend on previously achieved steps, and there are planning limitations stemming from the hardware dependency and real-life scenario tests that are needed to validate the system.

The group will not have a de-facto project leader, given the divide-and-conquer strategy described above, however within each sub-group there may be individualized leadership and strategizing. Overall, the team will hold daily meetings in which the status of each sub-group of people will be explained and inter-modular planning will occur based on results. At the same time, one person will be assigned to the role of main team communicator. They will communicate with the clients about the project developments.

### 4.2 Time and Planning

Milestones:

1) Contact the company and receive the robot and documentation
2) Define user requirements
3) Successfully create the robot simulation environment
4) Mapping an environment and transmit it to the server
5) Object recognition and localization by 1 robot
6) Communicate with multiple robots
7) Merging the mapping, and object recognition localization with multiple robots.
8) Delivery of final products and report

## 5. Risks

There are always project risks during the duration of the project. Not all these risks can be avoided. Identifying risks in time can negate much of the negative consequences of the risk. Achieving this requires that potential risk is known, and how to combat the consequences of each of them.

### 5.1 Project Risks

Not all risk can be identified or are worth mentioning. Therefore, some common risks are mentioned.

- Not enough time. Due to the lack of time, one or more requirements cannot be met.
- No clear project objective. The objective should be crystal clear to every member of the group.
| This is needed to work towards the same goals.
- Communication problems. Communication is key in group projects. Improper communication can
| lead to delays in the project
- Incomplete project planning. An incomplete planning can lead to more work required that
| predicted in the beginning.
- Absence of project members.
- Absence of project tutor.
- insufficient support external companies
- COVID-19 Lockdowns
- Delayed arrival of goods
- Poor performance of group member(s)

### 5.2 Risk Classification

Classifying risk is done using the impact of the risk when things go wrong, and the chance this events occurs. The impact is measured in the amount of time lost, because time is one of the most important resources during projects. The multiplication of these two factors determines the risk degree. Besides the risk degree the risk priority is useful the know. This can be quantified by multiplying the risk impact with the vulnerability you have for the risk. This can be summarized in the following formulas:

Risk = Risk impact × Probability

Risk priority = Risk × Vulnerbility

Rating | Name | Progress loss
1 | Incidental | Less than a day
2 | Minor | One day to one week
3 | Medium | One to two weeks
4 | Major | Two weeks to a month
5 | Extreme | More than one month
Table 3: Impact scale

Rating | Name | Chance of occurrence during project
1 | Incidental | 0 – 10%
2 | Minor | 10 – 25%
3 | Medium | 25 – 50%
4 | Major | 50 – 75%
5 | Extreme | 75 – 100%
Table 4 Probability scale
Rating | Name | Description
1 | Incidental | Almost no impact on project result
2 | Minor | No severe impact on project result
3 | Medium | Project result at risk
4 | Major | Serious risk for project
5 | Extreme | Fatal risk for project
Table 5 Vulerability scale
Risk | I | P | V | Risk degree | Risk priority
Not enough time | 4 | 3 | 4 | 12 | 48
No clear project objective | 2 | 2 | 1 | 4 | 4
Communication problems | 1 | 1 | 2 | 1 | 2
Incomplete project planning | 2 | 2 | 1 | 4 | 4
Absence of project members | 3 | 1 | 2 | 3 | 6
Absence of project tutor. | 2 | 1 | 1 | 2 | 2
insufficient support external companies | 2 | 2 | 2 | 4 | 8
COVID-19 Lockdowns | 4 | 2 | 3 | 8 | 24
Delayed arrival of goods | 2 | 3 | 2 | 6 | 12
Poor performance of group member(s) | 2 | 1 | 2 | 2 | 4

Table 6: Classification of risks

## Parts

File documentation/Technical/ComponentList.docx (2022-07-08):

Wheels 120mm

https://www.conrad.nl/nl/p/reely-buggy-complete-wielen-sand-schijf-zwart-2-stuk-s-235783.html

Back wheel 60 mm diameter

https://nl.rs-online.com/web/p/castor-wheels/4589642

Motor Driver 2x

https://www.tinytronics.nl/shop/en/mechanics-and-actuators/motor-controllers-and-drivers/stepper-motor-controllers-and-drivers/drv8825-motor-driver-module

Stepper Motor 2x

https://www.tinytronics.nl/shop/en/mechanics-and-actuators/motors/stepper-motors/stepper-motor-0.41n.m-1.7a-nema17

Raspberry pi zero 2 w

https://www.conrad.nl/nl/p/raspberry-pi-zero-2-w-raspberry-pi-zero-2-w-512-mb-1-x-2-4-ghz-2482940.html

360 Lidar

https://nl.rs-online.com/web/p/sensor-development-tools/2037609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

Lipo battery 2200ah or bigger

https://nl.rs-online.com/web/p/rechargeable-battery-packs/1449413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

TX60 stekker

https://www.conrad.nl/nl/p/reely-adapterkabel-1x-ec5-stekker-1x-xt60-bus-10-00-cm-re-6903786-2301262.html

Stepdown converter

https://www.tinytronics.nl/shop/en/power/voltage-converters/buck-(step-down)-converters/dc-dc-ajustable-step-down-buck-converter-lm2596-3a

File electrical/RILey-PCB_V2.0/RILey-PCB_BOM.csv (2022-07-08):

Qty | Value | Device | Package | Parts | Description | ALLIED_NUMBER | ARROW_PART_NUMBER | ARROW_PRICE-STOCK | CATEGORY | COLOR | CONNECTOR_TYPE | CONTACT_FINISH | CONTACT_FINISH_THICKNESS | CONTACT_MATING_LENGTH | CONTACT_TYPE | DESCRIPTION | DOCUMENTATION_LINK | DOCUMENTATION_URL | FAMILY | FASTENING_TYPE | FEATURES | HEIGHT | MANUFACTURER | MANUFACTURER_NAME | MANUFACTURER_PART_NUMBER | MF | MOUNTING_TYPE | MOUSER_PART_NUMBER | MOUSER_PRICE-STOCK | MPN | NUMBER_OF_POSITIONS | NUMBER_OF_POSITIONS_LOADED | NUMBER_OF_ROWS | OC_FARNELL | OC_NEWARK | PART_NUMBER | PITCH | POPULARITY | ROW_SPACING | RS_PART_NUMBER | RS_PRICE-STOCK | SERIES | SUPPLIER_ITEM_LINK | SUPPLIER_ITEM_NUMBER | SUPPLIER_ITEM_URL | SUPPLIER_LINK | SUPPLIER_NAME | SUPPLIER_URL | TERMINATION
1 |  | ELECTROLYTIC_CAPACITOR'8*20' | ELECTROLYTIC_CAPACITOR | C5
1 |  | FE04-1 | FE04-1 | PMETER | FEMALE HEADER
4 |  | W237-102 | W237-102 | BUCK_IN, BUCK_OUT, CURR_SENSE, VOLT_SENSE | WAGO SCREW CLAMP |  |  |  |  |  |  |  |  |  |  |  |  |  |  |  |  |  |  |  |  |  |  |  |  | 237-102 |  |  |  | unknown | 70K9898 |  |  | 32
2 | 26604020 | 26604020 | KK41791-4020_2-PIN | BATTERY1, BATTERY2 | KK® 396 Header, Vertical, Friction Lock, 2 Circuits, Tin (Sn) Plating |  |  |  | Connectors, Interconnects | Natural | Header, Unshrouded | Tin | 60µin (1.52µm) | 0.450 (11.43mm)" | Male Pin | CONN HEADER 2POS .156 VERT TIN | <a href=http://www.molex.com/pdm_docs/sd/026604020_sd.pdf">Datasheet</a>" | http://www.molex.com/pdm_docs/sd/026604020_sd.pdf | Rectangular Connectors - Headers, Male Pins | Friction Lock | - |  | Molex Inc |  |  |  | Through Hole |  |  |  | 2 | All | 1 |  |  | 26604020 | 0.156 (3.96mm)" |  | - |  |  | KK® 41791 | <a href=http://www.digikey.com/product-search/en?KeyWords=0026604020&WT.z_header=search_go">Details</a>" | WM4620-ND | http://www.digikey.com/product-search/en?KeyWords=0026604020&WT.z_header=search_go | <a href=http://www.digikey.com">Home Page</a>" | Digi-Key | http://www.digikey.com | Solder
2 | 100uF | UPS1E101MED | CAPPRD250W50D655H1250 | C1, C2 | Al electrolytic cap,PS,25V,100 F Nichicon 100uF 25 V dc Aluminium Electrolytic Capacitor, PS Series 2000h 6.3 (Dia.) x 11mm | 70187653 |  |  |  |  |  |  |  |  |  | Al electrolytic cap,PS,25V,100 F Nichicon 100uF 25 V dc Aluminium Electrolytic Capacitor, PS Series 2000h 6.3 (Dia.) x 11mm |  |  |  |  |  | 12.5mm |  | Nichicon | UPS1E101MED |  |  |  |  |  |  |  |  |  |  |  |  |  |  | 5194059P | http://uk.rs-online.com/web/p/products/5194059P
1 | 1101M2S3CQE2 | 1101M2S3CQE2 | 1000-SERIES(SPDT) | S1 | 1101M2S3CQE2 (Slide Switches) | 70128282 |  |  |  |  |  |  |  |  |  | 1101M2S3CQE2 (Slide Switches) |  |  |  |  |  | mm |  | C & K COMPONENTS | 1101M2S3CQE2 |  |  |  |  |  |  |  |  |  |  |  |  |  |  | 1617340 | http://uk.rs-online.com/web/p/products/1617340
1 | 1812L300MR | 1812L300MR | 1812L300MR | F2
1 | 2920L400/15MR | 2920L400/15MR | 2920L400/15MR | F1
2 | B4B-XH-A_LF__SN_ | B4B-XH-A_LF__SN_ | B4B-XH-A_LF__SN_ | MCONN1, MCONN2 | XH-2.5mm Header top entry 4 way JST XH Series, Series Number B4B, 2.5mm Pitch 4 Way 1 Row Straight PCB Header, Solder Termination, 3A |  |  |  |  |  |  |  |  |  |  | XH-2.5mm Header top entry 4 way JST XH Series, Series Number B4B, 2.5mm Pitch 4 Way 1 Row Straight PCB Header, Solder Termination, 3A |  |  |  |  |  | 7mm |  | JST (JAPAN SOLDERLESS TERMINALS) | B4B-XH-A(LF)(SN)
1 | DC_BARREL0-62 | DC_BARREL0-62 | 733980-62 | BARREL | FEMALE PRINT CONNECTOR |  |  |  |  |  |  |  |  |  |  |  |  |  |  |  |  |  |  |  |  |  |  |  |  |  |  |  |  |  |  |  |  | 0
1 | DIODE-BRIGDE | DIODE-BRIGDE | DIODE-BRIDGE | D2
4 | FE08-1_3D | FE08-1_3D | FE08-1 | MDRIVER_1A, MDRIVER_1B, MDRIVER_2A, MDRIVER_2B | FEMALE HEADER
1 | FE10-1_3D | FE10-1_3D | FE10-1 | IMU | FEMALE HEADER
1 | MA04-1W | MA04-1W | MA04-1W | TOF | PIN HEADER
4 | MA04-1_SMALLPAD | MA04-1_SMALLPAD | MA04-1_S | FUT_5V, FUT_GND, FUT_I2C_SCL, FUT_I2C_SDA | PIN HEADER
1 | MA05-1_SMALLPAD | MA05-1_SMALLPAD | MA05-1_S | LIDAR | PIN HEADER
1 | MA15-1W | MA15-1W | MA15-1W | GPIO_PINS | PIN HEADER
1 | MC-254-40-00-ST-DIP | MC-254-40-00-ST-DIP | MC-254-40-00-ST-DIP | J1 | CONNECTOR, HEADER, 40POS, 2ROW, 2.54MM; Pitch Spacing:2.54mm; No. of Contacts:40Contacts; Gender:Header; Product Range:-; Contact Termination Type:Through Hole; No. of Rows:2Rows; Contact Plating:Gold Plated Contacts RoHS Compliant: Yes |  |  |  |  |  |  |  |  |  |  | CONNECTOR, HEADER, 40POS, 2ROW, 2.54MM | Pitch Spacing:2.54mm | No. of Contacts:40Contacts | Gender:Header | Product Range:- | Contact Termination Type:Through Hole | No. of Rows:2Rows | Contact Plating:Gold Plated Contacts RoHS Compliant: Yes |  |  |  |  |  | 9.1mm |  | MULTICOMP | MC-254-40-00-ST-DIP
1 | SI2303CDS-T1-GE3 | PMN30UNH | TSOP6_SOT457 | MOSFET1
0,23 | ZENER-THDO-35 | ZENER-THDO-35 | ZENER-TH | D1

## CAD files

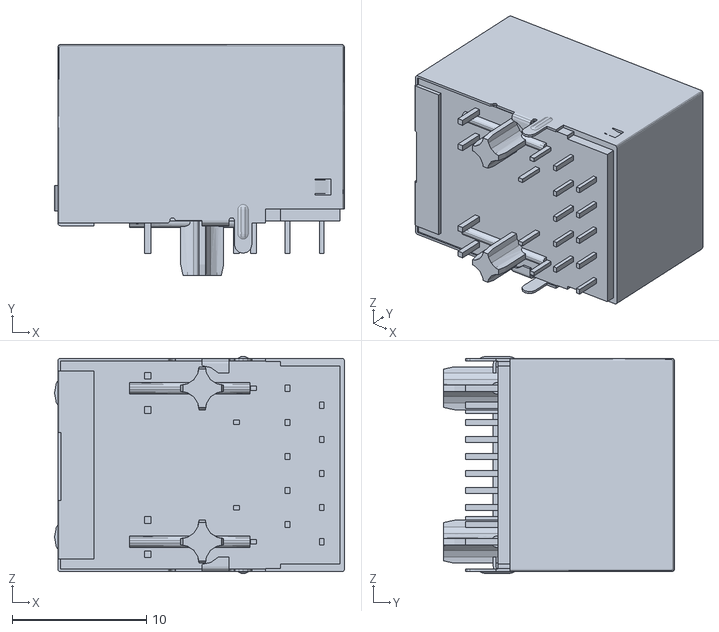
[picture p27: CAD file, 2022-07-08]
ros2/simulation/rileyRobot_ws/install/my_riley_robot_description/share/my_riley_robot_description/meshes/RILey_assembly - Raspberry Pi 4 Model B-1 Gigabit Ethernet Port, RPi4ModelB-1.STL
21.6 x 17.2 x 16.2

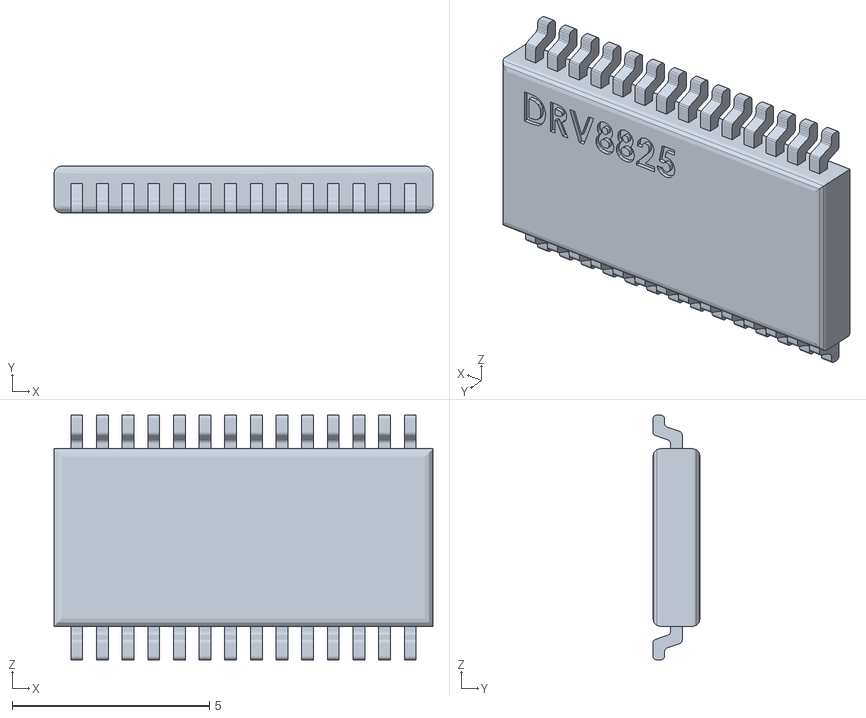
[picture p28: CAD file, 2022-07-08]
ros2/simulation/rileyRobot_ws/src/my_riley_robot_description/meshes/RILey_assembly - PCB-1 DRV 8825 With Headers Assem-4 DRV8825 IC-1.STL
9.60 x 1.20 x 6.20

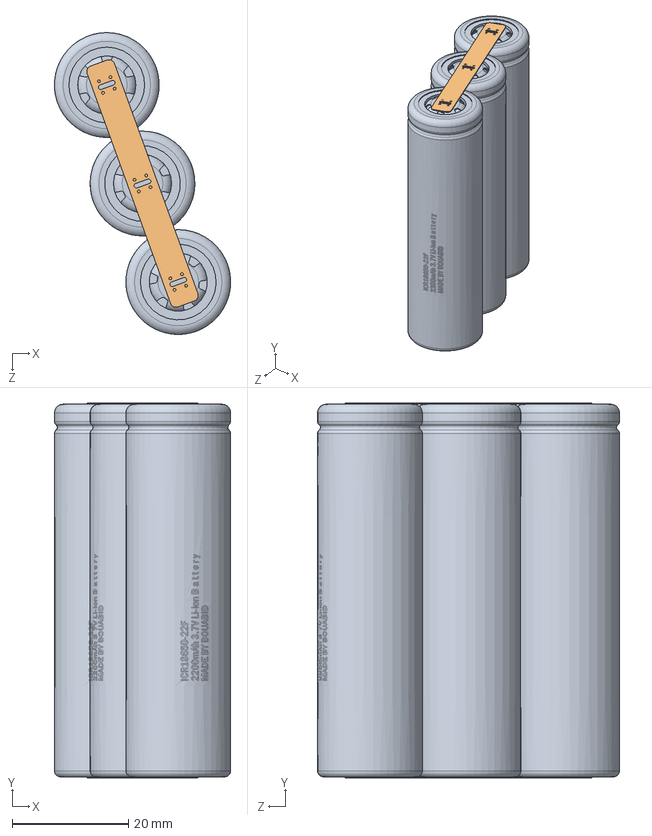
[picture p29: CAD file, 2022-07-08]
solidworks/Imported/Battery3cell/3_battery_pack.SLDASM
30.3 x 64.4 x 51.8 mm
Li-ion Battery x 3
link2 x 2

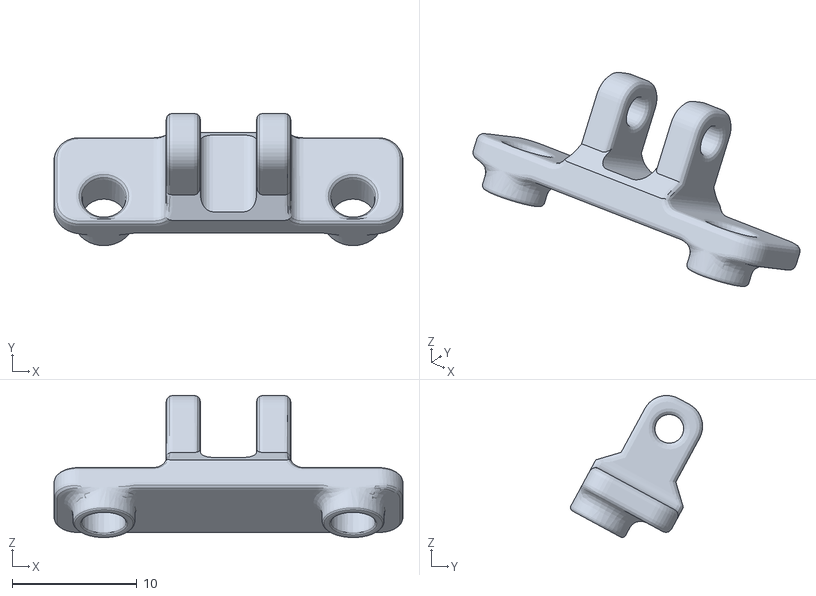
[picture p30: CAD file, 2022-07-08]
ros2/riley_ws/src/my_riley_robot_description/meshes/RILey_assembly - TimeOfFlightMount-1.STL
28.0 x 10.6 x 11.4

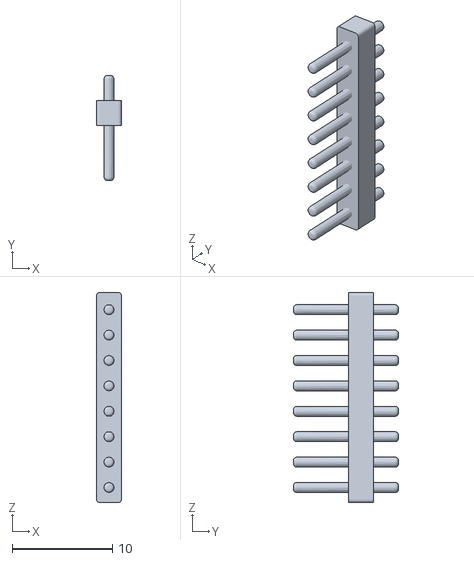
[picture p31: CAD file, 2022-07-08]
ros2/simulation/rileyRobot_ws/src/my_riley_robot_description/meshes/RILey_assembly - PCB-1 DRV 8825 With Headers Assem-4 8 pin Header-2.STL
2.50 x 10.5 x 21.0

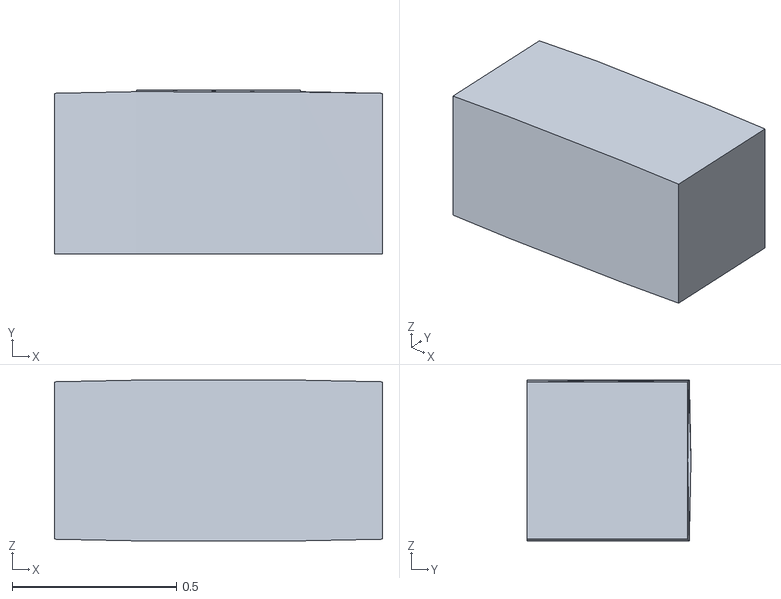
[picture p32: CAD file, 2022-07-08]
ros2/riley_ws/src/my_riley_robot_description/meshes/RILey_assembly - PCB-1 DRV 8825 With Headers Assem-4 0402 Resistor-1.STL
1.00 x 0.5 x 0.49

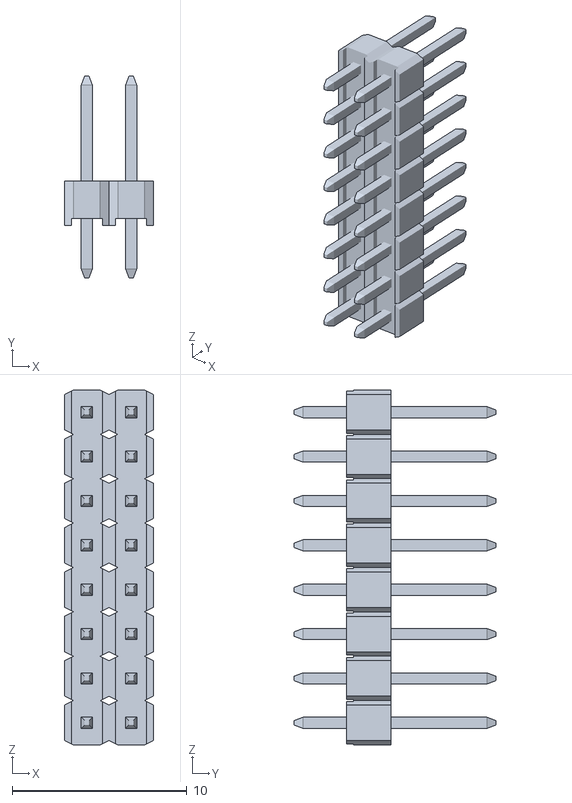
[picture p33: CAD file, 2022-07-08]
ros2/simulation/rileyRobot_ws/install/my_riley_robot_description/share/my_riley_robot_description/meshes/RILey_assembly - PCB-1 PinHeader2x8row-2.STL
5.08 x 11.5 x 20.3

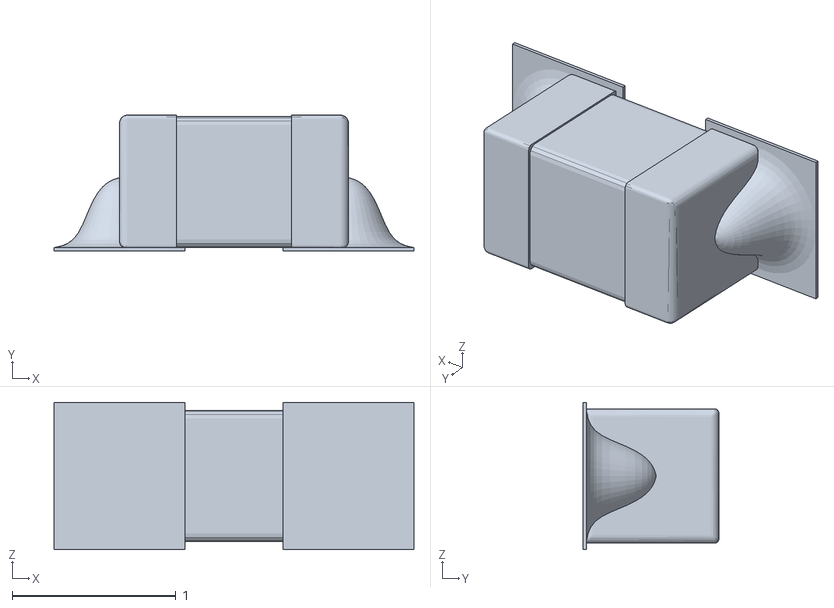
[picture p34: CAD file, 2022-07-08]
ros2/simulation/rileyRobot_ws/src/my_riley_robot_description/meshes/RILey_assembly - PCB-1 MPU9250.STEP-1 C1_Predeterminado_Como mecanizada_.STEP-2.STL
2.20 x 0.83 x 0.9

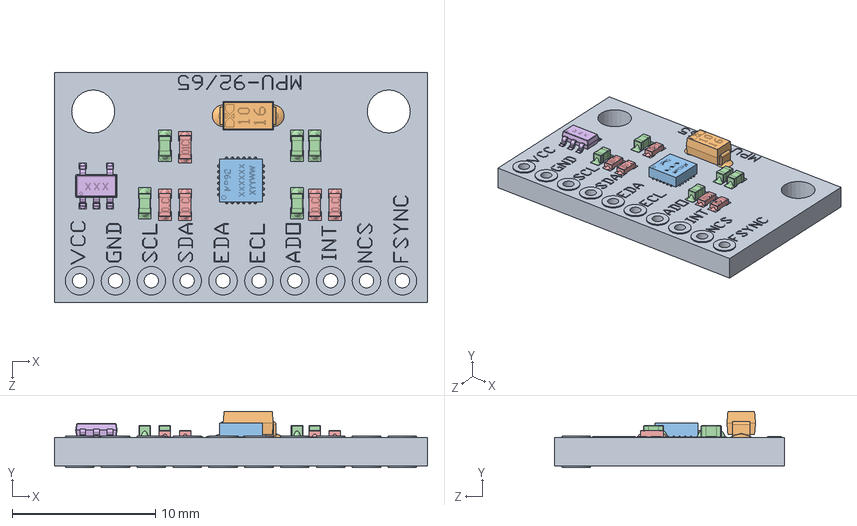
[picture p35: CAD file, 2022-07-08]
solidworks/Imported/mpu-92-65-1.snapshot.2/MPU 92_65/MPU9250.SLDASM
26.0 x 3.91 x 16.0 mm
PCB
C2
MP92
C1 x 5
R1 x 5
V1

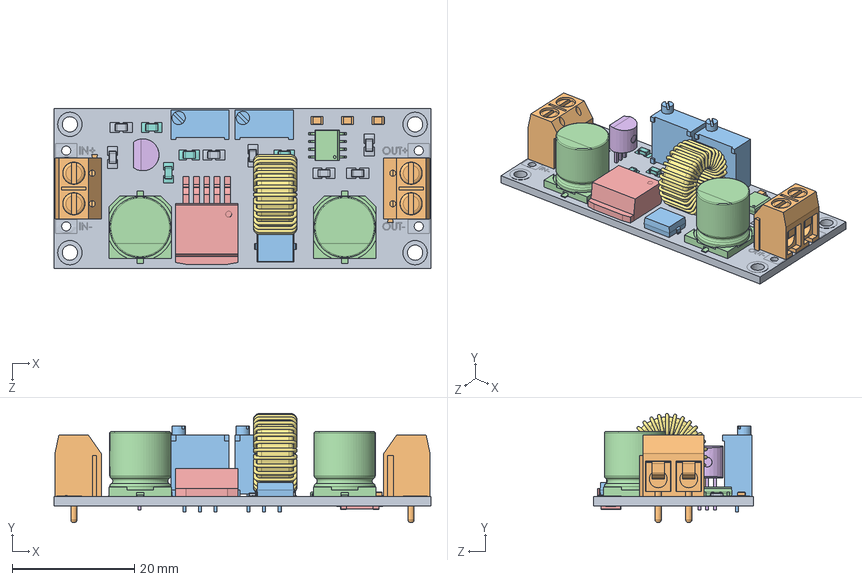
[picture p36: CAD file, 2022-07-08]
solidworks/Imported/xl4015-5a-dc-dc-cc-cv-buck-converter-1.snapshot.14/pack-n-go/dc-dc-5a-cc.SLDASM
61.7 x 17.9 x 26.2 mm
PCB^dc-dc-5a-cc
DG301-5.0-02 x 2
Trimpot 3296W x 2
CAPACITOR 10x10 SMD x 2
XL4015E1
LM317LZ
coil^dc-dc-5a-cc
C x 4
R x 8
LED x 3
D
SO-8
Rshunt^dc-dc-5a-cc

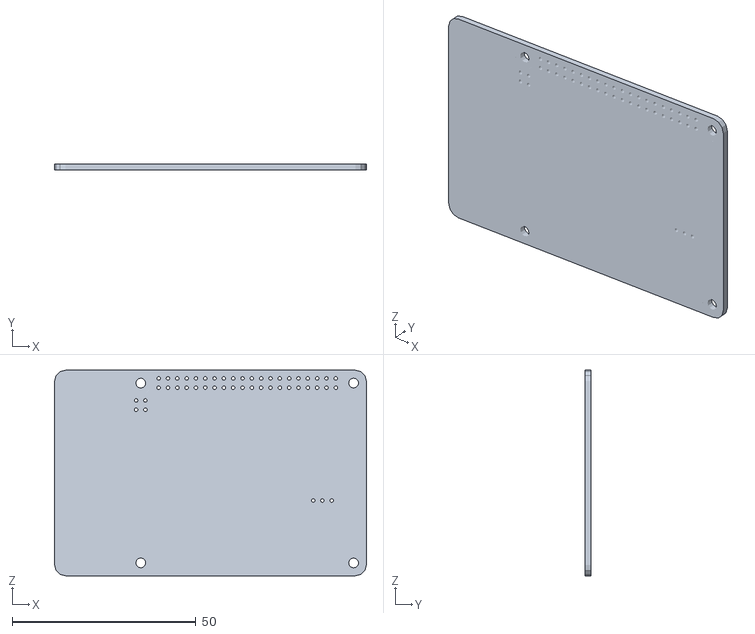
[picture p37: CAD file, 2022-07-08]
ros2/riley_ws/src/my_riley_robot_description/meshes/RILey_assembly - Raspberry Pi 4 Model B-1 PCB, RPi4ModelB-1.STL
85.0 x 1.60 x 56.0

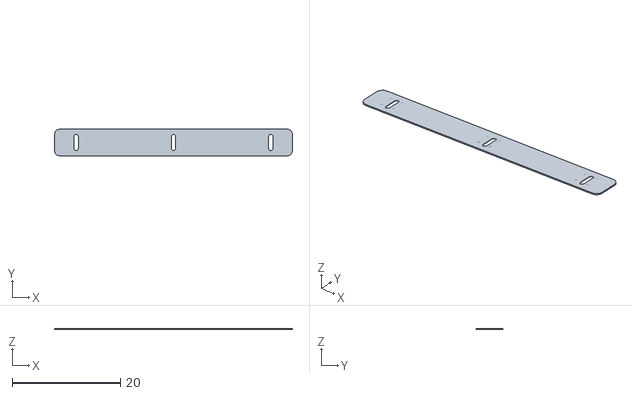
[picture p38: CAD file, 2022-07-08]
ros2/simulation/rileyRobot_ws/src/my_riley_robot_description/meshes/RILey_assembly - 3_battery_pack-2 link2-1.STL
44.0 x 5.00 x 0.2

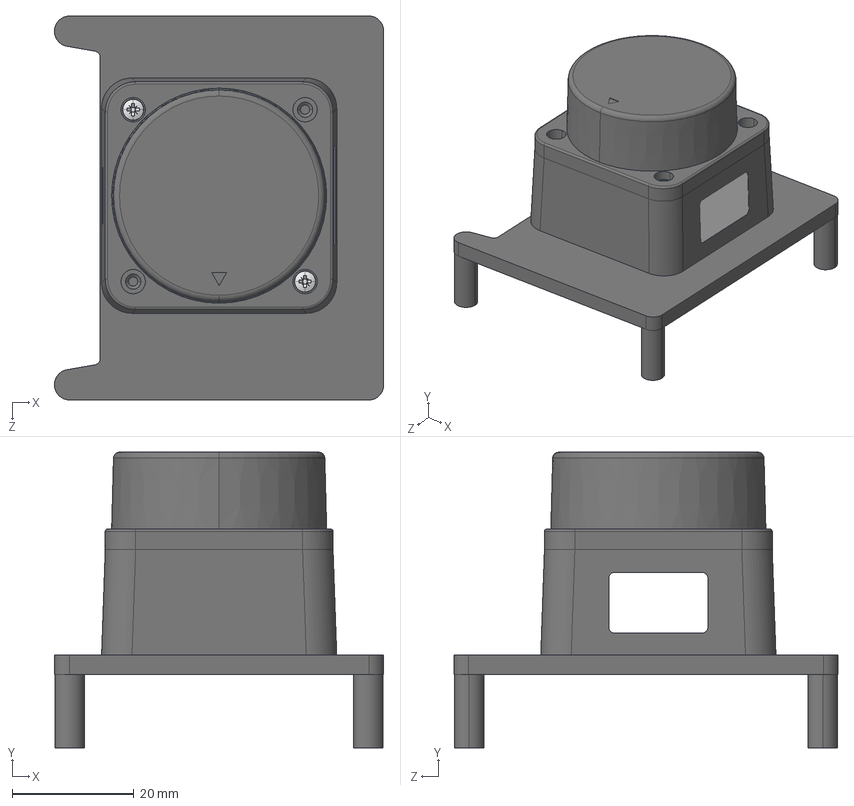
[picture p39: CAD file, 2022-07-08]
solidworks/Imported/ldrobot-ld06-360-lidar-module-raspberry-pi-mounting-bracket-1.snapshot.4/LD06_Assembly.STEP
54.0 x 48.5 x 63.0 mm
LD06_LiDAR
JIS_B1111_M2x6.step x 2
jst-1.5mm-4P.step
LD06_PiBracket

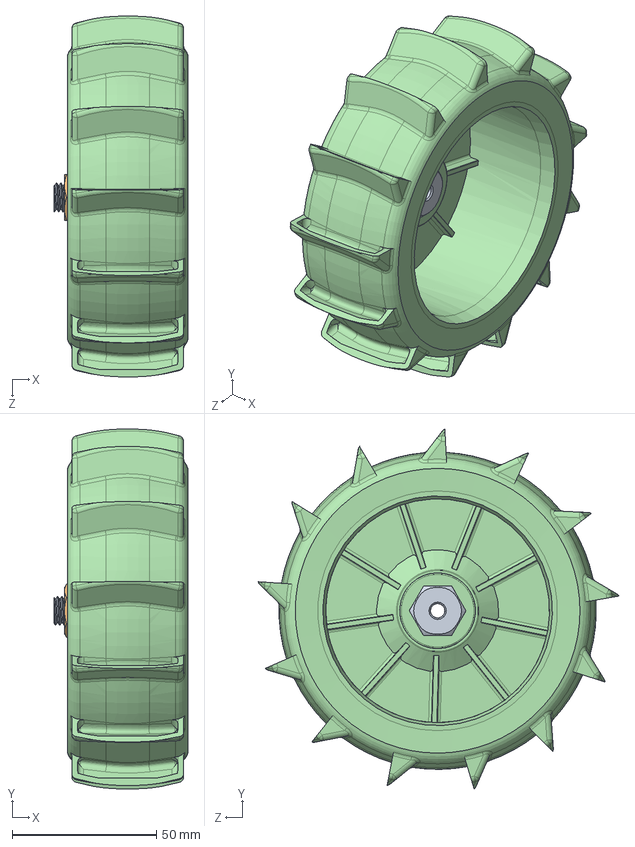
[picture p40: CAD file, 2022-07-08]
solidworks/RILey V2/LeftWheelAssembly.SLDASM
46.3 x 124.7 x 125.0 mm
HexBolt_modified
hex nut style 1 gradeab_din
socket set screw cup point_din
ReelyBuggyWheel_Left

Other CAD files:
ros2/riley_ws/src/my_riley_robot_description/meshes/RILey_assembly - PCB-1 DRV 8825 With Headers Assem-2 0402 Resistor-6.STL
ros2/simulation/rileyRobot_ws/install/my_riley_robot_description/share/my_riley_robot_description/meshes/RILey_assembly - PCB-1 DRV 8825 With Headers Assem-4 0402 Resistor-4.STL
ros2/simulation/rileyRobot_ws/install/my_riley_robot_description/share/my_riley_robot_description/meshes/RILey_assembly - 3_battery_pack-1 Li-ion Battery-2.STL
electrical/RILey-PCB_V1.0/RILey_PCB.step
electrical/RILey-PCB_V2.0/Eagle_Fusion-Files/RILey-PCB_V2.0_v99.f3z
electrical/RILey-PCB_V2.0/RILey-PCB_V2.0.step
ros2/riley_ws/src/my_riley_robot_description/meshes/RILey_assembly - 3_battery_pack-1 Li-ion Battery-1.STL
ros2/riley_ws/src/my_riley_robot_description/meshes/RILey_assembly - 3_battery_pack-1 Li-ion Battery-2.STL
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

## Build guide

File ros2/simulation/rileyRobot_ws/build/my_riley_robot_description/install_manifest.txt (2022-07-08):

/home/student/rileyRobot_ws/install/my_riley_robot_description/share/my_riley_robot_description//launch/spawn_riley_robot_v2.py
/home/student/rileyRobot_ws/install/my_riley_robot_description/share/my_riley_robot_description//launch/publish_urdf.launch.py
/home/student/rileyRobot_ws/install/my_riley_robot_description/share/my_riley_robot_description//launch/spawn_riley_robot_launch.py
/home/student/rileyRobot_ws/install/my_riley_robot_description/share/my_riley_robot_description//launch/spawn_riley_robot.py
/home/student/rileyRobot_ws/install/my_riley_robot_description/share/my_riley_robot_description//launch/multi_riley_robot.launch.py
/home/student/rileyRobot_ws/install/my_riley_robot_description/share/my_riley_robot_description//launch/display.launch.py
/home/student/rileyRobot_ws/install/my_riley_robot_description/share/my_riley_robot_description//Riley_URDF/riley_robot_original.urdf.xacro
/home/student/rileyRobot_ws/install/my_riley_robot_description/share/my_riley_robot_description//Riley_URDF/riley_robot.urdf
/home/student/rileyRobot_ws/install/my_riley_robot_description/share/my_riley_robot_description//Riley_URDF/riley_robot.urdf.xacro
/home/student/rileyRobot_ws/install/my_riley_robot_description/share/my_riley_robot_description//rviz/urdf.rviz
/home/student/rileyRobot_ws/install/my_riley_robot_description/share/my_riley_robot_description//meshes/RILey_assembly - Raspberry Pi 4 Model B-1 2.54 mm DUPONT MALE PIN HEADER, IO, 2X20, RPi4ModelB-1.STL
/home/student/rileyRobot_ws/install/my_riley_robot_description/share/my_riley_robot_description//meshes/RILey_assembly - PCB-1 MPU9250.STEP-1 C1_Predeterminado_Como mecanizada_.STEP-5.STL
/home/student/rileyRobot_ws/install/my_riley_robot_description/share/my_riley_robot_description//meshes/RILey_assembly - hex nut style 1 gradeab_din-18.STL
/home/student/rileyRobot_ws/install/my_riley_robot_description/share/my_riley_robot_description//meshes/RILey_assembly - Raspberry Pi 4 Model B-1 Display Connector, RPi4ModelB-1.STL
/home/student/rileyRobot_ws/install/my_riley_robot_description/share/my_riley_robot_description//meshes/RILey_assembly - PCB-1 MPU9250.STEP-1 V1.STEP-1.STL
/home/student/rileyRobot_ws/install/my_riley_robot_description/share/my_riley_robot_description//meshes/RILey_assembly - PCB-1 DRV 8825 With Headers Assem-2 0402 Resistor-7.STL
/home/student/rileyRobot_ws/install/my_riley_robot_description/share/my_riley_robot_description//meshes/RILey_assembly - PCB-1 zl262-8s_p2-54_l20-8_w2-54_h8-5.stp-1.STL
/home/student/rileyRobot_ws/install/my_riley_robot_description/share/my_riley_robot_description//meshes/RILey_assembly - PCB-1 MPU9250.STEP-1 R1.STEP-4.STL
/home/student/rileyRobot_ws/install/my_riley_robot_description/share/my_riley_robot_description//meshes/RILey_assembly - 3_battery_pack-2 link2-1.STL
/home/student/rileyRobot_ws/install/my_riley_robot_description/share/my_riley_robot_description//meshes/RILey_assembly - ReelyBuggyWheel_Left-2.STL
/home/student/rileyRobot_ws/install/my_riley_robot_description/share/my_riley_robot_description//meshes/RILey_assembly - socket head cap screw 4762_din-7.STL
/home/student/rileyRobot_ws/install/my_riley_robot_description/share/my_riley_robot_description//meshes/RILey_assembly - PCB-1 DRV 8825 With Headers Assem-4 0402 Resistor-3.STL
/home/student/rileyRobot_ws/install/my_riley_robot_description/share/my_riley_robot_description//meshes/RILey_assembly - socket head cap screw 4762_din-42.STL
/home/student/rileyRobot_ws/install/my_riley_robot_description/share/my_riley_robot_description//meshes/RILey_assembly - PCB-1 MPU9250.STEP-1 R1.STEP-3.STL
/home/student/rileyRobot_ws/install/my_riley_robot_description/share/my_riley_robot_description//meshes/RILey_assembly - 3rdFloor_Sheetmetal-1.STL
/home/student/rileyRobot_ws/install/my_riley_robot_description/share/my_riley_robot_description//meshes/RILey_assembly - socket head cap screw 4762_din-46.STL
/home/student/rileyRobot_ws/install/my_riley_robot_description/share/my_riley_robot_description//meshes/RILey_assembly - PCB-1 DRV 8825 With Headers Assem-2 0402 Resistor-1.STL
/home/student/rileyRobot_ws/install/my_riley_robot_description/share/my_riley_robot_description//meshes/RILey_assembly - socket head cap screw 4762_din-4.STL
/home/student/rileyRobot_ws/install/my_riley_robot_description/share/my_riley_robot_description//meshes/RILey_assembly - Raspberry Pi 4 Model B-1 Microphone Plug, RPi4ModelB-1.STL
/home/student/rileyRobot_ws/install/my_riley_robot_description/share/my_riley_robot_description//meshes/RILey_assembly - PCB-1 MPU9250.STEP-1 C1_Predeterminado_Como mecanizada_.STEP-4.STL
/home/student/rileyRobot_ws/install/my_riley_robot_description/share/my_riley_robot_description//meshes/RILey_assembly - socket head cap screw 4762_din-27.STL
/home/student/rileyRobot_ws/install/my_riley_robot_description/share/my_riley_robot_description//meshes/RILey_assembly - PCB-1 zl262-8s_p2-54_l20-8_w2-54_h8-5.stp-7.STL
/home/student/rileyRobot_ws/install/my_riley_robot_description/share/my_riley_robot_description//meshes/RILey_assembly - hex nut style 1 gradeab_iso-3.STL
/home/student/rileyRobot_ws/install/my_riley_robot_description/share/my_riley_robot_description//meshes/RILey_assembly - Nema 17_Slim-2.STL
/home/student/rileyRobot_ws/install/my_riley_robot_description/share/my_riley_robot_description//meshes/RILey_assembly - socket head cap screw 4762_din-41.STL
/home/student/rileyRobot_ws/install/my_riley_robot_description/share/my_riley_robot_description//meshes/RILey_assembly - PCB-1 DRV 8825 With Headers Assem-2 0603 Resistor-2.STL
/home/student/rileyRobot_ws/install/my_riley_robot_description/share/my_riley_robot_description//meshes/RILey_assembly - Spacer-6.STL
/home/student/rileyRobot_ws/install/my_riley_robot_description/share/my_riley_robot_description//meshes/RILey_assembly - PCB-1 Platine 5x7.stp-1.STL
/home/student/rileyRobot_ws/install/my_riley_robot_description/share/my_riley_robot_description//meshes/RILey_assembly - hex nut style 1 gradeab_din-8.STL
/home/student/rileyRobot_ws/install/my_riley_robot_description/share/my_riley_robot_description//meshes/RILey_assembly - 3_battery_pack-2 link2-2.STL
/home/student/rileyRobot_ws/install/my_riley_robot_description/share/my_riley_robot_description//meshes/RILey_assembly - hex screw gradeab fine_iso-2.STL
/home/student/rileyRobot_ws/install/my_riley_robot_description/share/my_riley_robot_description//meshes/RILey_assembly - PCB-1 DRV 8825 With Headers Assem-4 0402 Resistor-1.STL
/home/student/rileyRobot_ws/install/my_riley_robot_description/share/my_riley_robot_description//meshes/RILey_assembly - socket head cap screw 4762_din-66.STL
/home/student/rileyRobot_ws/install/my_riley_robot_description/share/my_riley_robot_description//meshes/RILey_assembly - socket head cap screw 4762_din-51.STL
/home/student/rileyRobot_ws/install/my_riley_robot_description/share/my_riley_robot_description//meshes/RILey_assembly - Raspberry Pi 4 Model B-1 Broadcom BCM2711B0 CPU, RPi4ModelB-1.STL
/home/student/rileyRobot_ws/install/my_riley_robot_description/share/my_riley_robot_description//meshes/RILey_assembly - PCB-1 DRV 8825 With Headers Assem-4 8 pin Header-1.STL
/home/student/rileyRobot_ws/install/my_riley_robot_description/share/my_riley_robot_description//meshes/RILey_assembly - hex nut style 1 gradeab_din-7.STL
/home/student/rileyRobot_ws/install/my_riley_robot_description/share/my_riley_robot_description//meshes/RILey_assembly - socket head cap screw 4762_din-47.STL
/home/student/rileyRobot_ws/install/my_riley_robot_description/share/my_riley_robot_description//meshes/RILey_assembly - socket head cap screw 4762_din-22.STL
/home/student/rileyRobot_ws/install/my_riley_robot_description/share/my_riley_robot_description//meshes/RILey_assembly - Cam V2.1 v1.step-1.STL
/home/student/rileyRobot_ws/install/my_riley_robot_description/share/my_riley_robot_description//meshes/RILey_assembly - socket head cap screw_iso-13.STL
/home/student/rileyRobot_ws/install/my_riley_robot_description/share/my_riley_robot_description//meshes/RILey_assembly - 3_battery_pack-1 link2-1.STL
/home/student/rileyRobot_ws/install/my_riley_robot_description/share/my_riley_robot_description//meshes/RILey_assembly - PCB-1 zl262-8s_p2-54_l20-8_w2-54_h8-5.stp-5.STL
/home/student/rileyRobot_ws/install/my_riley_robot_description/share/my_riley_robot_description//meshes/RILey_assembly - socket head cap screw 4762_din-33.STL
/home/student/rileyRobot_ws/install/my_riley_robot_description/share/my_riley_robot_description//meshes/RILey_assembly - PCB-1 PinHeader2x8row-2.STL
/home/student/rileyRobot_ws/install/my_riley_robot_description/share/my_riley_robot_description//meshes/RILey_assembly - CameraMount-1.STL
/home/student/rileyRobot_ws/install/my_riley_robot_description/share/my_riley_robot_description//meshes/RILey_assembly - PCB-1 MPU9250.STEP-1 MP92.STEP-1.STL
/home/student/rileyRobot_ws/install/my_riley_robot_description/share/my_riley_robot_description//meshes/RILey_assembly - socket head cap screw 4762_din-2.STL
/home/student/rileyRobot_ws/install/my_riley_robot_description/share/my_riley_robot_description//meshes/RILey_assembly - socket head cap screw 4762_din-26.STL
/home/student/rileyRobot_ws/install/my_riley_robot_description/share/my_riley_robot_description//meshes/RILey_assembly - PCB-1 MPU9250.STEP-1 C1_Predeterminado_Como mecanizada_.STEP-3.STL
/home/student/rileyRobot_ws/install/my_riley_robot_description/share/my_riley_robot_description//meshes/RILey_assembly - Raspberry Pi 4 Model B-1 2.54 mm DUPONT MALE PIN HEADER, POE, 2X2, RPi4ModelB-1.STL
/home/student/rileyRobot_ws/install/my_riley_robot_description/share/my_riley_robot_description//meshes/RILey_assembly - dc-dc-5a-cc-merged-1.STL
/home/student/rileyRobot_ws/install/my_riley_robot_description/share/my_riley_robot_description//meshes/RILey_assembly - socket head cap screw 4762_din-58.STL
/home/student/rileyRobot_ws/install/my_riley_robot_description/share/my_riley_robot_description//meshes/RILey_assembly - 3_battery_pack-1 Li-ion Battery-3.STL
/home/student/rileyRobot_ws/install/my_riley_robot_description/share/my_riley_robot_description//meshes/RILey_assembly - socket head cap screw 4762_din-32.STL
/home/student/rileyRobot_ws/install/my_riley_robot_description/share/my_riley_robot_description//meshes/RILey_assembly - PCB-1 MPU9250.STEP-1 C1_Predeterminado_Como mecanizada_.STEP-2.STL
/home/student/rileyRobot_ws/install/my_riley_robot_description/share/my_riley_robot_description//meshes/RILey_assembly - socket head cap screw_iso-15.STL
/home/student/rileyRobot_ws/install/my_riley_robot_description/share/my_riley_robot_description//meshes/RILey_assembly - Raspberry Pi 4 Model B-1 Female USB Type C Connector, RPi4ModelB-1.STL
/home/student/rileyRobot_ws/install/my_riley_robot_description/share/my_riley_robot_description//meshes/RILey_assembly - socket head cap screw 4762_din-53.STL
/home/student/rileyRobot_ws/install/my_riley_robot_description/share/my_riley_robot_description//meshes/RILey_assembly - PCB-1 DRV 8825 With Headers Assem-2 0402 Resistor-2.STL
/home/student/rileyRobot_ws/install/my_riley_robot_description/share/my_riley_robot_description//meshes/RILey_assembly - PCB-1 PinHeader8row-3.STL
/home/student/rileyRobot_ws/install/my_riley_robot_description/share/my_riley_robot_description//meshes/RILey_assembly - VL53l1X-1.STL
/home/student/rileyRobot_ws/install/my_riley_robot_description/share/my_riley_robot_description//meshes/RILey_assembly - TimeOfFlightMount-1.STL
/home/student/rileyRobot_ws/install/my_riley_robot_description/share/my_riley_robot_description//meshes/RILey_assembly - 3_battery_pack-2 Li-ion Battery-3.STL
/home/student/rileyRobot_ws/install/my_riley_robot_description/share/my_riley_robot_description//meshes/RILey_assembly - socket head cap screw 4762_din-62.STL
/home/student/rileyRobot_ws/install/my_riley_robot_description/share/my_riley_robot_description//meshes/RILey_assembly - PCB-1 DRV 8825 With Headers Assem-2 0402 Resistor-3.STL
/home/student/rileyRobot_ws/install/my_riley_robot_description/share/my_riley_robot_description//meshes/RILey_assembly - Spacer-4.STL
/home/student/rileyRobot_ws/install/my_riley_robot_description/share/my_riley_robot_description//meshes/RILey_assembly - PCB-1 DRV 8825 With Headers Assem-2 8 pin Header-1.STL
/home/student/rileyRobot_ws/install/my_riley_robot_description/share/my_riley_robot_description//meshes/RILey_assembly - Spacer-3.STL
/home/student/rileyRobot_ws/install/my_riley_robot_description/share/my_riley_robot_description//meshes/RILey_assembly - PCB-1 DRV 8825 With Headers Assem-2 0402 Resistor-5.STL
/home/student/rileyRobot_ws/install/my_riley_robot_description/share/my_riley_robot_description//meshes/RILey_assembly - socket head cap screw 4762_din-9.STL
/home/student/rileyRobot_ws/install/my_riley_robot_description/share/my_riley_robot_description//meshes/RILey_assembly - PCB-1 DRV 8825 With Headers Assem-4 0402 Resistor-2.STL
/home/student/rileyRobot_ws/install/my_riley_robot_description/share/my_riley_robot_description//meshes/RILey_assembly - hex nut style 1 gradeab_din-16.STL
/home/student/rileyRobot_ws/install/my_riley_robot_description/share/my_riley_robot_description//meshes/RILey_assembly - LD06_Assembly-1 LD06_LiDAR-1 JIS_B1111_M2x6.step-1.STL
/home/student/rileyRobot_ws/install/my_riley_robot_description/share/my_riley_robot_description//meshes/RILey_assembly - LD06_Assembly-1 LD06_LiDAR-1 LD06_LiDAR-1.STL
/home/student/rileyRobot_ws/install/my_riley_robot_description/share/my_riley_robot_description//meshes/RILey_assembly - socket head cap screw 4762_din-61.STL
/home/student/rileyRobot_ws/install/my_riley_robot_description/share/my_riley_robot_description//meshes/RILey_assembly - PCB-1 DRV 8825 With Headers Assem-2 8 pin Header-2.STL
/home/student/rileyRobot_ws/install/my_riley_robot_description/share/my_riley_robot_description//meshes/RILey_assembly - 3_battery_pack-1 link2-2.STL
/home/student/rileyRobot_ws/install/my_riley_robot_description/share/my_riley_robot_description//meshes/RILey_assembly - socket head cap screw 4762_din-54.STL
/home/student/rileyRobot_ws/install/my_riley_robot_description/share/my_riley_robot_description//meshes/RILey_assembly - socket head cap screw 4762_din-48.STL
/home/student/rileyRobot_ws/install/my_riley_robot_description/share/my_riley_robot_description//meshes/RILey_assembly - hex nut style 1 gradeab_din-13.STL
/home/student/rileyRobot_ws/install/my_riley_robot_description/share/my_riley_robot_description//meshes/RILey_assembly - socket head cap screw_iso-3.STL
/home/student/rileyRobot_ws/install/my_riley_robot_description/share/my_riley_robot_description//meshes/RILey_assembly - ReelyBuggyWheel_Right-2.STL
/home/student/rileyRobot_ws/install/my_riley_robot_description/share/my_riley_robot_description//meshes/RILey_assembly - hex nut style 1 gradeab_iso-2.STL
/home/student/rileyRobot_ws/install/my_riley_robot_description/share/my_riley_robot_description//meshes/RILey_assembly - PCB-1 DRV 8825 With Headers Assem-4 0402 Resistor-7.STL
/home/student/rileyRobot_ws/install/my_riley_robot_description/share/my_riley_robot_description//meshes/RILey_assembly - Spacer-5.STL
/home/student/rileyRobot_ws/install/my_riley_robot_description/share/my_riley_robot_description//meshes/RILey_assembly - PCB-1 DRV 8825 With Headers Assem-2 DRV8825 IC-1.STL
/home/student/rileyRobot_ws/install/my_riley_robot_description/share/my_riley_robot_description//meshes/RILey_assembly - Backwheel-1.STL
/home/student/rileyRobot_ws/install/my_riley_robot_description/share/my_riley_robot_description//meshes/RILey_assembly - 3_battery_pack-2 Li-ion Battery-1.STL
/home/student/rileyRobot_ws/install/my_riley_robot_description/share/my_riley_robot_description//meshes/RILey_assembly - socket head cap screw 4762_din-59.STL
/home/student/rileyRobot_ws/install/my_riley_robot_description/share/my_riley_robot_description//meshes/RILey_assembly - Raspberry Pi 4 Model B-1 SD Card Slot, RPi4ModelB-1.STL
/home/student/rileyRobot_ws/install/my_riley_robot_description/share/my_riley_robot_description//meshes/RILey_assembly - Raspberry Pi 4 Model B-1 Broadcom BCM54213PE Gigabit Ethernet Transceiver, RPi4ModelB-1.STL
/home/student/rileyRobot_ws/install/my_riley_robot_description/share/my_riley_robot_description//meshes/RILey_assembly - PCB-1 B4B-XH-A.step-2.STL
/home/student/rileyRobot_ws/install/my_riley_robot_description/share/my_riley_robot_description//meshes/RILey_assembly - Raspberry Pi 4 Model B-1 Female Micro HDMI Connector, RPi4ModelB-2.STL
/home/student/rileyRobot_ws/install/my_riley_robot_description/share/my_riley_robot_description//meshes/RILey_assembly - PCB-1 DRV 8825 With Headers Assem-2 0603 Resistor-1.STL
/home/student/rileyRobot_ws/install/my_riley_robot_description/share/my_riley_robot_description//meshes/RILey_assembly - Spacer-7.STL
/home/student/rileyRobot_ws/install/my_riley_robot_description/share/my_riley_robot_description//meshes/RILey_assembly - hex nut style 1 gradeab_din-15.STL
/home/student/rileyRobot_ws/install/my_riley_robot_description/share/my_riley_robot_description//meshes/RILey_assembly - hex screw gradeab fine_iso-1.STL
/home/student/rileyRobot_ws/install/my_riley_robot_description/share/my_riley_robot_description//meshes/RILey_assembly - PCB-1 DRV 8825 With Headers Assem-2 0402 Resistor-6.STL
/home/student/rileyRobot_ws/install/my_riley_robot_description/share/my_riley_robot_description//meshes/RILey_assembly - PCB-1 PinHeader2x8row-1.STL
/home/student/rileyRobot_ws/install/my_riley_robot_description/share/my_riley_robot_description//meshes/RILey_assembly - PCB-1 DRV 8825 With Headers Assem-4 8 pin Header-2.STL
/home/student/rileyRobot_ws/install/my_riley_robot_description/share/my_riley_robot_description//meshes/RILey_assembly - PCB-1 MPU9250.STEP-1 C1_Predeterminado_Como mecanizada_.STEP-1.STL
/home/student/rileyRobot_ws/install/my_riley_robot_description/share/my_riley_robot_description//meshes/RILey_assembly - socket head cap screw 4762_din-16.STL
/home/student/rileyRobot_ws/install/my_riley_robot_description/share/my_riley_robot_description//meshes/RILey_assembly - PCB-1 DRV 8825 With Headers Assem-2 0402 Resistor-4.STL
/home/student/rileyRobot_ws/install/my_riley_robot_description/share/my_riley_robot_description//meshes/RILey_assembly - Raspberry Pi 4 Model B-1 Gigabit Ethernet Port, RPi4ModelB-1.STL
/home/student/rileyRobot_ws/install/my_riley_robot_description/share/my_riley_robot_description//meshes/RILey_assembly - Raspberry Pi 4 Model B-1 PCB, RPi4ModelB-1.STL
/home/student/rileyRobot_ws/install/my_riley_robot_description/share/my_riley_robot_description//meshes/RILey_assembly - LD06_Assembly-1 LD06_LiDAR-1 JIS_B1111_M2x6.step-2.STL
/home/student/rileyRobot_ws/install/my_riley_robot_description/share/my_riley_robot_description//meshes/RILey_assembly - PCB-1 DRV 8825 With Headers Assem-2 PCB-1.STL
/home/student/rileyRobot_ws/install/my_riley_robot_description/share/my_riley_robot_description//meshes/RILey_assembly - PCB-1 zl262-8s_p2-54_l20-8_w2-54_h8-5.stp-6.STL
/home/student/rileyRobot_ws/install/my_riley_robot_description/share/my_riley_robot_description//meshes/RILey_assembly - Raspberry Pi 4 Model B-1 2X USB3.0 PORTS, RPi4ModelB-2.STL
/home/student/rileyRobot_ws/install/my_riley_robot_description/share/my_riley_robot_description//meshes/RILey_assembly - LD06_Assembly-1 LD06_PiBracket-1.STL
/home/student/rileyRobot_ws/install/my_riley_robot_description/share/my_riley_robot_description//meshes/RILey_assembly - 3_battery_pack-1 Li-ion Battery-1.STL
/home/student/rileyRobot_ws/install/my_riley_robot_description/share/my_riley_robot_description//meshes/RILey_assembly - PCB-1 DRV 8825 With Headers Assem-4 SMD Pot-1.STL
/home/student/rileyRobot_ws/install/my_riley_robot_description/share/my_riley_robot_description//meshes/RILey_assembly - socket head cap screw_iso-16.STL
/home/student/rileyRobot_ws/install/my_riley_robot_description/share/my_riley_robot_description//meshes/RILey_assembly - hex nut style 1 gradeab_din-17.STL
/home/student/rileyRobot_ws/install/my_riley_robot_description/share/my_riley_robot_description//meshes/RILey_assembly - socket head cap screw_iso-2.STL
/home/student/rileyRobot_ws/install/my_riley_robot_description/share/my_riley_robot_description//meshes/RILey_assembly - socket head cap screw_iso-17.STL
/home/student/rileyRobot_ws/install/my_riley_robot_description/share/my_riley_robot_description//meshes/RILey_assembly - socket head cap screw 4762_din-6.STL
/home/student/rileyRobot_ws/install/my_riley_robot_description/share/my_riley_robot_description//meshes/RILey_assembly - hex nut style 1 gradeab_iso-5.STL
/home/student/rileyRobot_ws/install/my_riley_robot_description/share/my_riley_robot_description//meshes/RILey_assembly - socket head cap screw 4762_din-25.STL
/home/student/rileyRobot_ws/install/my_riley_robot_description/share/my_riley_robot_description//meshes/RILey_assembly - LD06_Assembly-1 LD06_LiDAR-1 jst-1.5mm-4P.step-1.STL
/home/student/rileyRobot_ws/install/my_riley_robot_description/share/my_riley_robot_description//meshes/RILey_assembly - PCB-1 MPU9250.STEP-1 R1.STEP-1.STL
/home/student/rileyRobot_ws/install/my_riley_robot_description/share/my_riley_robot_description//meshes/RILey_assembly - socket head cap screw_iso-9.STL
/home/student/rileyRobot_ws/install/my_riley_robot_description/share/my_riley_robot_description//meshes/RILey_assembly - socket head cap screw 4762_din-49.STL
/home/student/rileyRobot_ws/install/my_riley_robot_description/share/my_riley_robot_description//meshes/RILey_assembly - Raspberry Pi 4 Model B-1 Camera Connector, RPi4ModelB-1.STL
/home/student/rileyRobot_ws/install/my_riley_robot_description/share/my_riley_robot_description//meshes/RILey_assembly - BatteryCoverFront-1.STL
/home/student/rileyRobot_ws/install/my_riley_robot_description/share/my_riley_robot_description//meshes/RILey_assembly - socket head cap screw 4762_din-52.STL
/home/student/rileyRobot_ws/install/my_riley_robot_description/share/my_riley_robot_description//meshes/RILey_assembly - Raspberry Pi 4 Model B-1 91D77 D9WHV 778K, 4 GB LPDDR4 SDRAM, RPi4ModelB-1.STL
/home/student/rileyRobot_ws/install/my_riley_robot_description/share/my_riley_robot_description//meshes/RILey_assembly - Raspberry Pi 4 Model B-1 Female Micro HDMI Connector, RPi4ModelB-3.STL
/home/student/rileyRobot_ws/install/my_riley_robot_description/share/my_riley_robot_description//meshes/RILey_assembly - PCB-1 PinHeader10row-1.STL
/home/student/rileyRobot_ws/install/my_riley_robot_description/share/my_riley_robot_description//meshes/RILey_assembly - Spacer-2.STL
/home/student/rileyRobot_ws/install/my_riley_robot_description/share/my_riley_robot_description//meshes/RILey_assembly - Raspberry Pi 4 Model B-1 Cypress CYW43455 Wireless Module Cover, RPi4ModelB-1.STL
/home/student/rileyRobot_ws/install/my_riley_robot_description/share/my_riley_robot_description//meshes/RILey_assembly - socket head cap screw 4762_din-8.STL
/home/student/rileyRobot_ws/install/my_riley_robot_description/share/my_riley_robot_description//meshes/RILey_assembly - hex nut style 1 gradeab_din-11.STL
/home/student/rileyRobot_ws/install/my_riley_robot_description/share/my_riley_robot_description//meshes/RILey_assembly - PCB-1 MPU9250.STEP-1 R1.STEP-2.STL
/home/student/rileyRobot_ws/install/my_riley_robot_description/share/my_riley_robot_description//meshes/RILey_assembly - PCB-1 B4B-XH-A.step-1.STL
/home/student/rileyRobot_ws/install/my_riley_robot_description/share/my_riley_robot_description//meshes/RILey_assembly - Raspberry Pi 4 Model B-1 VIA VL805 PCIe USB 3.0 controller, RPi4ModelB-1.STL
/home/student/rileyRobot_ws/install/my_riley_robot_description/share/my_riley_robot_description//meshes/RILey_assembly - PCB-1 DRV 8825 With Headers Assem-4 0402 Resistor-6.STL
/home/student/rileyRobot_ws/install/my_riley_robot_description/share/my_riley_robot_description//meshes/RILey_assembly - Raspberry Pi 4 Model B-1 2X USB2.0 PORTS, RPi4ModelB-1.STL
/home/student/rileyRobot_ws/install/my_riley_robot_description/share/my_riley_robot_description//meshes/RILey_assembly - hex nut style 1 gradeab_din-10.STL
/home/student/rileyRobot_ws/install/my_riley_robot_description/share/my_riley_robot_description//meshes/RILey_assembly - PCB-1 DRV 8825 With Headers Assem-4 PCB-1.STL
/home/student/rileyRobot_ws/install/my_riley_robot_description/share/my_riley_robot_description//meshes/RILey_assembly - socket head cap screw 4762_din-43.STL
/home/student/rileyRobot_ws/install/my_riley_robot_description/share/my_riley_robot_description//meshes/RILey_assembly - PCB-1 DRV 8825 With Headers Assem-4 0603 Resistor-2.STL
/home/student/rileyRobot_ws/install/my_riley_robot_description/share/my_riley_robot_description//meshes/RILey_assembly - PCB-1 DRV 8825 With Headers Assem-2 SMD Pot-1.STL
/home/student/rileyRobot_ws/install/my_riley_robot_description/share/my_riley_robot_description//meshes/RILey_assembly - PCB-1 MPU9250.STEP-1 C2.STEP-1.STL
/home/student/rileyRobot_ws/install/my_riley_robot_description/share/my_riley_robot_description//meshes/RILey_assembly - hex nut style 1 gradeab_iso-4.STL
/home/student/rileyRobot_ws/install/my_riley_robot_description/share/my_riley_robot_description//meshes/RILey_assembly - PCB-1 zl262-8s_p2-54_l20-8_w2-54_h8-5.stp-2.STL
/home/student/rileyRobot_ws/install/my_riley_robot_description/share/my_riley_robot_description//meshes/RILey_assembly - PCB-1 DRV 8825 With Headers Assem-2 0805 Capacitor-1.STL
/home/student/rileyRobot_ws/install/my_riley_robot_description/share/my_riley_robot_description//meshes/RILey_assembly - MiddlepartV1-1.STL
/home/student/rileyRobot_ws/install/my_riley_robot_description/share/my_riley_robot_description//meshes/RILey_assembly - socket head cap screw 4762_din-3.STL
/home/student/rileyRobot_ws/install/my_riley_robot_description/share/my_riley_robot_description//meshes/RILey_assembly - PCB-1 DRV 8825 With Headers Assem-4 0402 Resistor-4.STL
/home/student/rileyRobot_ws/install/my_riley_robot_description/share/my_riley_robot_description//meshes/RILey_assembly - PCB-1 MPU9250.STEP-1 PCB.STEP-1.STL
/home/student/rileyRobot_ws/install/my_riley_robot_description/share/my_riley_robot_description//meshes/RILey_assembly - Spacer-8.STL
/home/student/rileyRobot_ws/install/my_riley_robot_description/share/my_riley_robot_description//meshes/RILey_assembly - socket head cap screw 4762_din-5.STL
/home/student/rileyRobot_ws/install/my_riley_robot_description/share/my_riley_robot_description//meshes/RILey_assembly - Nema 17_Slim-1.STL
/home/student/rileyRobot_ws/install/my_riley_robot_description/share/my_riley_robot_description//meshes/RILey_assembly - PCB-1 DRV 8825 With Headers Assem-4 DRV8825 IC-1.STL
/home/student/rileyRobot_ws/install/my_riley_robot_description/share/my_riley_robot_description//meshes/RILey_assembly - socket head cap screw 4762_din-40.STL
/home/student/rileyRobot_ws/install/my_riley_robot_description/share/my_riley_robot_description//meshes/RILey_assembly - PCB-1 DRV 8825 With Headers Assem-4 0805 Capacitor-1.STL
/home/student/rileyRobot_ws/install/my_riley_robot_description/share/my_riley_robot_description//meshes/RILey_assembly - 3_battery_pack-1 Li-ion Battery-2.STL
/home/student/rileyRobot_ws/install/my_riley_robot_description/share/my_riley_robot_description//meshes/RILey_assembly - 3_battery_pack-2 Li-ion Battery-2.STL
/home/student/rileyRobot_ws/install/my_riley_robot_description/share/my_riley_robot_description//meshes/RILey_assembly - Raspberry Pi 4 Model B-1 MxL7704 Universal PMIC, RPi4ModelB-1.STL
/home/student/rileyRobot_ws/install/my_riley_robot_description/share/my_riley_robot_description//meshes/RILey_assembly - PCB-1 zl262-4s_p2-54_l10-6_w2-54_h8-5.stp-1.STL
/home/student/rileyRobot_ws/install/my_riley_robot_description/share/my_riley_robot_description//meshes/RILey_assembly - hex nut style 1 gradeab_din-12.STL
/home/student/rileyRobot_ws/install/my_riley_robot_description/share/my_riley_robot_description//meshes/RILey_assembly - PCB-1 DRV 8825 With Headers Assem-4 0603 Resistor-1.STL
/home/student/rileyRobot_ws/install/my_riley_robot_description/share/my_riley_robot_description//meshes/RILey_assembly - Spacer-1.STL
/home/student/rileyRobot_ws/install/my_riley_robot_description/share/my_riley_robot_description//meshes/RILey_assembly - PCB-1 PinHeader8row-1.STL
/home/student/rileyRobot_ws/install/my_riley_robot_description/share/my_riley_robot_description//meshes/RILey_assembly - hex nut style 1 gradeab_din-20.STL
/home/student/rileyRobot_ws/install/my_riley_robot_description/share/my_riley_robot_description//meshes/RILey_assembly - PCB-1 MPU9250.STEP-1 R1.STEP-5.STL
/home/student/rileyRobot_ws/install/my_riley_robot_description/share/my_riley_robot_description//meshes/RILey_assembly - PCB-1 DRV 8825 With Headers Assem-4 0402 Resistor-5.STL
/home/student/rileyRobot_ws/install/my_riley_robot_description/share/my_riley_robot_description//config/nav2_params.yaml
/home/student/rileyRobot_ws/install/my_riley_robot_description/share/my_riley_robot_description//config/ekf.yaml
/home/student/rileyRobot_ws/install/my_riley_robot_description/share/my_riley_robot_description//worlds/riley_robot_empty.world
/home/student/rileyRobot_ws/install/my_riley_robot_description/share/my_riley_robot_description//worlds/my_world.sdf
/home/student/rileyRobot_ws/install/my_riley_robot_description/lib/my_riley_robot_description/spawn_riley_robot.py
/home/student/rileyRobot_ws/install/my_riley_robot_description/lib/my_riley_robot_description/spawn_riley_robot_v2.py
/home/student/rileyRobot_ws/install/my_riley_robot_description/share/ament_index/resource_index/package_run_dependencies/my_riley_robot_description
/home/student/rileyRobot_ws/install/my_riley_robot_description/share/ament_index/resource_index/parent_prefix_path/my_riley_robot_description
/home/student/rileyRobot_ws/install/my_riley_robot_description/share/my_riley_robot_description/environment/ament_prefix_path.sh
/home/student/rileyRobot_ws/install/my_riley_robot_description/share/my_riley_robot_description/environment/ament_prefix_path.dsv
/home/student/rileyRobot_ws/install/my_riley_robot_description/share/my_riley_robot_description/environment/path.sh
/home/student/rileyRobot_ws/install/my_riley_robot_description/share/my_riley_robot_description/environment/path.dsv
/home/student/rileyRobot_ws/install/my_riley_robot_description/share/my_riley_robot_description/local_setup.bash
/home/student/rileyRobot_ws/install/my_riley_robot_description/share/my_riley_robot_description/local_setup.sh
/home/student/rileyRobot_ws/install/my_riley_robot_description/share/my_riley_robot_description/local_setup.zsh
/home/student/rileyRobot_ws/install/my_riley_robot_description/share/my_riley_robot_description/local_setup.dsv
/home/student/rileyRobot_ws/install/my_riley_robot_description/share/my_riley_robot_description/package.dsv
/home/student/rileyRobot_ws/install/my_riley_robot_description/share/ament_index/resource_index/packages/my_riley_robot_description
/home/student/rileyRobot_ws/install/my_riley_robot_description/share/my_riley_robot_description/cmake/my_riley_robot_descriptionConfig.cmake
/home/student/rileyRobot_ws/install/my_riley_robot_description/share/my_riley_robot_description/cmake/my_riley_robot_descriptionConfig-version.cmake
/home/student/rileyRobot_ws/install/my_riley_robot_description/share/my_riley_robot_description/package.xml

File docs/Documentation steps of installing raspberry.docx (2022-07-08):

Goal is to install ROS2 on raspberry

Following this tutorial https://roboticsbackend.com/install-ros2-on-raspberry-pi/

Downloading first Ubuntu use the official Raspberry Pi Imager (v1.7.2) and choose Ubuntu Server 20.04.4 LTS (RPI 3/4/400 64-bit)

Then insert SD card back in pc again to setup Wi-Fi and check ssh is enabled.

Then put it in the raspberry pi and change password. You need probably reboot it then again to connect it to the Wi-Fi. After that you can ssh into the pi

Then follow the tutorial again from: https://roboticsbackend.com/install-ros2-on-raspberry-pi/

For setting up an static IP on the raspberry follow this tutorial: https://linuxconfig.org/how-to-configure-static-ip-address-on-ubuntu-18-04-bionic-beaver-linux

libraries to install:

Install python3

Install pip3 for python3

Install rpi.gpio

Install thread6

Install sshkeyboard

Install vl53l1x

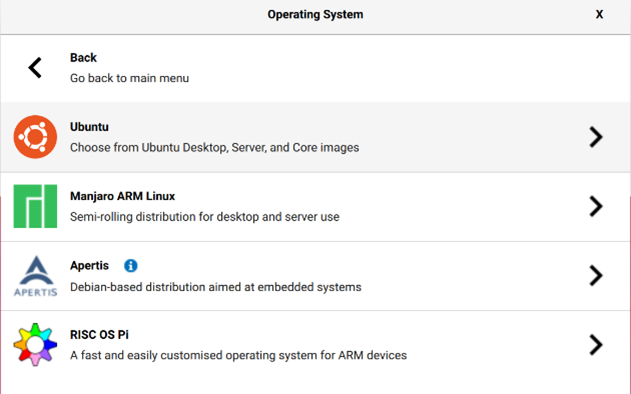
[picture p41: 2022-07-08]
docs/Environment_Preparations_RILey/pictures/Raspberry_Install/Raspberry_imager_pic2.png

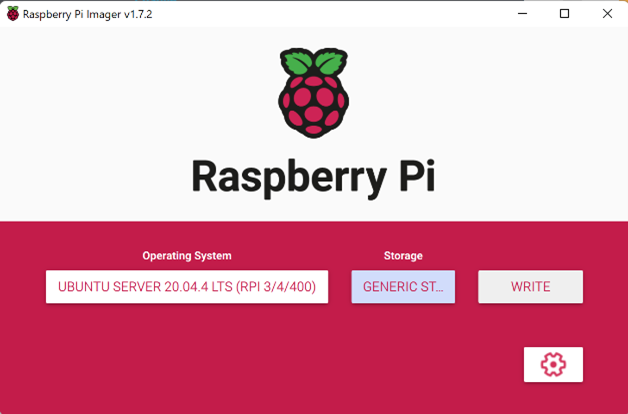
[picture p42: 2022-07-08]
docs/Environment_Preparations_RILey/pictures/Raspberry_Install/Raspberry_imager_pic4.png

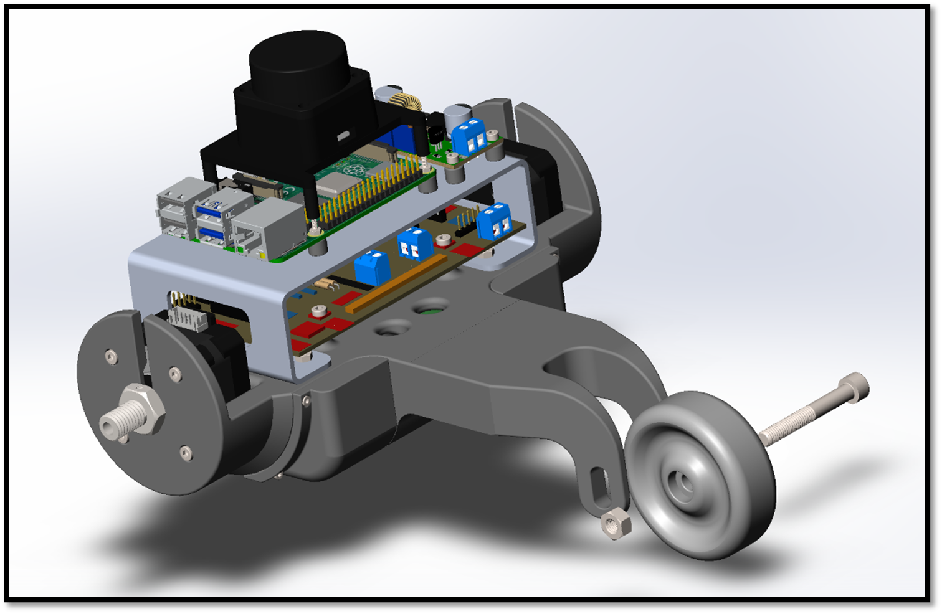
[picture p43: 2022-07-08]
docs/Environment_Preparations_RILey/pictures/LEGO_Assembly/Step15.png

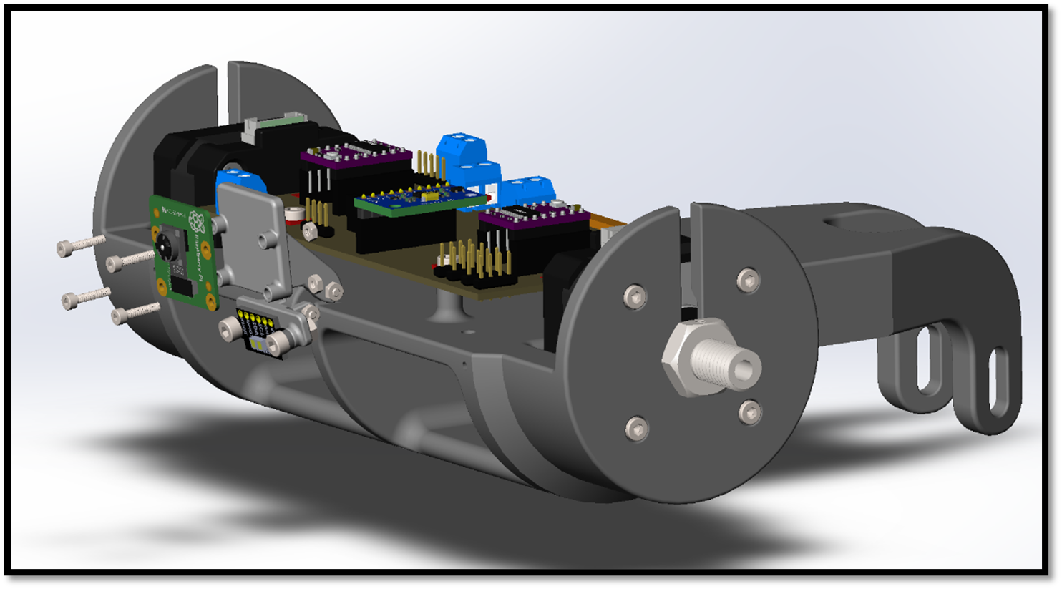
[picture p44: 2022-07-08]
docs/Environment_Preparations_RILey/pictures/LEGO_Assembly/Step9.png

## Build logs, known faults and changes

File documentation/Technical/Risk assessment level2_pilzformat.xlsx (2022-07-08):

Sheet: Section 1 & 2
1. DOCUMENT IDENTIFICATION
 | Document Identification
 | Project Name | RILey |  | Project No. | RILey001
 | Version | 1 |  | Date | 2022-05-16
 |  | Name |  | Signature |  | Date
 | Author | Alexandru Pășescu |  |  |  | 2022-05-16
 | Author | Quinvey Etienne |  |  |  | 2022-05-16
 | Author | Martijn Strolenberg |  |  |  | 2022-05-16
 | Author | Niels van Hinsberg |  |  |  | 2022-05-16
 | Author | Toby van Dueren den Hollander |  |  |  | 2022-05-16
 | Reviewed by | Reviewer |  | X |  | xx-xx-xxxx
 | Revision | Description |  | Changed by |  | Date
 | A | Initial Draft |  | All |  | 2022-05-16
2.1 PROJECT INFORMATION
 | MACHINE INFORMATION
 | Machine Name: |  | RILey Robot
 | Manufacturer: |  | Team RILey
 | Machine Type: |  | Reconnaissance Robot
 | Serial Number: |  | 1
 | Date of Manufacture: |  | 2022-05-09
 | Machine Certification: |  | N/a
 | DEVICE INFORMATION
 | Device Name: |  | RILey Robot
 | Manufacturer: |  | Team RILey
 | Device Type: |  | Reconnaissance Robot
 | Serial Number: |  | 1
 | Date of Manufacture: |  | 2022-05-09
 | Device Certification: |  | N/a
 | ASSESSMENT PERSONNEL / ASSESSMENT DATE
 | Initial Risk Assessment
 | Author: |  | Alexandru Pășescu |  | Date: | 2022-05-16
 | Author: |  | Quinvey Etienne |  | Date: | 2022-05-16
 | Author: |  | Martijn Strolenberg |  | Date: | 2022-05-16
 | Author: |  | Niels van Hinsberg |  | Date: | 2022-05-16
 | Author: |  | Toby van Dueren den Hollander |  | Date: | 2022-05-16
 | CUSTOMER PERSONNEL
 | Name: | Sjriek Alers |  | Function/ Job Title: |  | Lecturer, Client
 | Name: | Danny Hameeteman |  | Function/ Job Title: |  | Engineer, Project holder
2.3 METHOD OF RISK ANALYSIS
 | In accordance with ISO 12100, the risk assessment is implemented in a series of logical steps to enable a systematic examination of the hazards associated with machinery. Risk assessment is followed, whenever necessary by risk reduction as described in clause 6 of ISO 12100: 2010. When this process is repeated it gives an iterative process for eliminating hazards as far as possible and for implementing safety measures.
 | The risk assessment methodology approach includes: -- Risk analysis o Determination of limits o Hazard identification o Risk estimation -- Risk evaluation
 | The risk assessment provides the information required for the risk evaluation, which in turn allows judgements to be made on the safety of machinery.
 | The Diagram 1 shows the step-by-step process of risk analysis:
 | Diagram 1: Method of risk reduction
2.4 LIMIT OF REPORT
 | This risk assessment report is based on information that was accumulated during the on-site risk assessment of the RILey Robot at Fontys University of Applied Sciences on the 16-05-2022.
 | This risk assessment for work equipment examines significant hazards where risk reduction measures still need to be applied.
 | The information was accumulated in the following fashion: 1. Reviewing all available machine technical information 2. Conducting a physical examination of the machine
 | In order to ensure the accuracy of the risk assessment for the machine, it is imperative that the information provided on the date of the risk assessment be correct and reliable. Team RILey cannot take any responsibility for judgements made on inaccurate or lack of information.
 | Every effort is made to evaluate the risk associated with each hazard identified throughout the report, however it may not be possible to quantify the risk with all hazards. When this is not possible the hazards are assessed in relation to their conformance with all relevant Legislation. Each hazard is identified individually throughout the report; the outcome from the accumulation of hazards has not been evaluated.
 | Human error and misuse related to areas such as incorrect feeding of the machine, incorrect use of materials and operator ability to operate the machine are not considered to be under the scope of this report. Only clear foreseen misuse of the machine was considered.
 | Due to practical reasons not all the machine lifecycle was examined as part of this report, the following phases were excluded: - Assembly Installation - Decommissioning - Disposal - Transport - Construction - Commissioning

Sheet: Section 3
3. MACHINE ASSESSMENT
3.1 BASIC MACHINE DESCRIPTION
 | The RILey robot is used as an autonomous reconnaissance platform for scanning (un)known locations suchs as buildings. This scanning task is performed by combining sensory data, and sending this to a remote server where this data can be processed and interpreted. The platform is powered by two motors which are connected to large wheels which also provide the damping of the platform.
 | Visualising the surroundings is accomplished by using a camera feed in combination with LIDAR and Time of flight sensor. The operator must be able to end the autonomous operation at any time, and resume operation via manual commands.
 | Because the platform is power by Li-ion battery packs, the operating time is around 1 hour.
 | [place photo here]
 | Picture 1: Robotic cell used for risk assessment example
3.2 MACHINE CONTROL SYSTEM DESCRIPTION
 | The RILey robot is controlled by a Raspberry Pi model 4B. This controller controls the two stepper motors.
3.3 MACHINE SPECIFICATION
 | MACHINE LIMITS
 | Machine Name/Type |  | RILey Robot
 | Intended Environment: |  | Indoor
 | Required Training Level: |  | Basic Training
 | Operated by: |  | Operator, Maintenance Technician
 | Machine Lifetime: |  | 6 - 12 months
 | Machine Dimensions: |  | 230mm x 253mm x 155 mm
 | Machine Environment: |  | dry, clean, non explosive, non flammable.
 | OPERATIONAL AND MAINTENANCE INFORMATION
 | Operational Information
 | Emergency Stopping Time: |  | << 1 sec
 | Machine Cycle Time: |  | << 1 m/s
 | No. of Operators: |  | 1 in normal use
 | Maintenance Information
 | Maintened by: |  | Team RILey
 | Maintenance Frequency: |  | Not required
 | Cleaning: |  | No cleaning required
 | Jamming Repair: |  | Team RILey
 | POWER SOURCES
 | Control, Elec. Supply: |  | 2x 12V DC LI-ION battery pack
3.4 RISK ESTIMATION & EVALUATION CRITERIA
 | The Evaluation methodology is based on Pilz criteria and experience, an evaluation of the factors, Degree of Possible Harm (DPH), Probability of Occurrence of a Hazardous Event (PO), Possibility of Avoidance (PA) and Frequency and/or duration of Exposure (FE), and has been performed on the risk related with each hazard. A Pilz Hazard Rating has then been calculated from the following formula:
 | PHR = DPH x PO x PA x FE
 | Where the above parameters can take the following values:
 | Degree of Possible Harm (DPH) 0.25 Scratch / Bruise 0.5 Laceration / cut / mild ill health effect/ minor burns 3 Fracture minor bone – fingers, toes 5 Fracture major bone – hand, arm, leg 8 Loss of 1 or 2 fingers/ toes or major burns 11 Leg / hand amputation, partial loss of hearing or eye 15 Amputation of 2 legs/hands, total loss of hearing/sight in both ears/eyes 25 Critical injuries or permanent illness/condition/injury 40 Single Fatality 65 Catastrophe
 | Possibility of Occurrence of Hazard Event (PO) 0.05 Almost impossible 1.25 Unlikely 2.5 Possible 4 Probable 6 Certain
 | Possibility of Avoidance (PA) 0.75 Possible 2.5 Possible under certain circumstances 5 Not Possible
 | Frequency of Exposure (FE) 0.5 Annually 1 Monthly 2 Weekly 3 Daily 4 Hourly 5 Constantly
 | The maximum and minimum numerical values that could be assigned to each factor for every hazard are shown in the following table.
 | PHR |  | Risk |  | Comment
 |  | 1-10 | Negligible Risk |  | Presents practically no risk to health and safety, no further risk reduction measures are required.
 |  | 11-20 | Very Low Risk |  | Presents very little risk to health and safety, no significant risk reduction measures are required, may necessitate the use of personal protective equipment and/or training.
 |  | 21-45 | Low Risk |  | Risk to health and safety is present, but low. Risk reduction measures must be considered.
 |  | 46-160 | Significant Risk |  | The risk associated with the hazard is substantial enough to require risk reduction measures. These measures should be implemented at the next suitable opportunity.
 |  | 161-500 | High Risk |  | Potentially dangerous hazard, which requires risk reduction measures to be implemented urgently.
 |  | 501+ | Very high Risk |  | Risk reduction measures should be implemented immediately, corporate management should be notified.
 | Table X: PHR Numeric Range
 | After a complete examination of the machine based on applicable standards, a numerical value was determined for each factor while conducting the Risk Assessment and the Pilz Hazard Rating was calculated. The calculated number was then used to evaluate the risk associated with the hazard by comparison with predetermined acceptable levels.
 | The calculated Pilz Hazard Rating ranges from 1 to 9750 where 1 is the lowest showing minimum and 9750 is the highest risk.
3.5 Findings
 | Hazard Identification |  |  |  |  |  | Hazard No. | 1.1
 | Title | Falling Hazard
 | Location | Everywhere
 | Target | Head, shoulders, arms and feet
 | Activity | Normal operation
 | Task | Driving
 | Sub Task | Both Autonomous and Manual driving
 | Hazard Type | Mechanical Hazard with the consequence of collision
 | Description
 | References:
 | Risk Estimation and Evaluation
 | Degree of Possible Harm: |  |  | 25 | Possibility of Avoidance: |  |  | 0.75
 | Probability of Occurance of a Hazardous Event: |  |  | 2 | Frequency And/or Duration of Exposure: |  |  | 5
 | Pilz Hazard Rating (PHR): |  |  | 187.5 | Summary Level: |  | High Risk
 | Risk Reduction |  |  |  |  |  | Reference
 | Nessecery, add a time of flight sensor so it can detect a cliff and will stop before it falls off.
 | Risk Estimation and Evaluation
 | Degree of Possible Harm: |  |  | 25 | Possibility of Avoidance: |  |  | 0.75
 | Probability of Occurance of a Hazardous Event: |  |  | 0.05 | Frequency And/or Duration of Exposure: |  |  | 0.5
 | Pilz Hazard Rating (PHR): |  |  | 0.46875 | Summary Level: |  | Negligible Risk
 | Hazard Identification |  |  |  |  |  | Hazard No. | 1.2
 | Title | Tripping
 | Location | Everywhere
 | Target | Entire body
 | Activity | Normal operation
 | Task | Driving
 | Sub task
 | Hazard Type | Mechanical Hazard with the consequence of physical damage
 | Sub Type | Crushing and impact (Quasi-static)
 | Description | A person can trip over the robot. This can result in physical damage to the robot and the person.
 | References:
 | Risk Estimation and Evaluation
 | Degree of Possible Harm: |  |  | 25 | Possibility of Avoidance: |  |  | 0.75
 | Probability of Occurance of a Hazardous Event: |  |  | 4 | Frequency And/or Duration of Exposure: |  |  | 1
 | Pilz Hazard Rating (PHR): |  |  | 75 | Summary Level: |  | Significant Risk
 | Risk Reduction |  |  |  |  |  | Reference
 | The robot has a Time of Flight sensor and a Lidar witch can sense if a object is infront of the robot. It will stop or drive around the detected object / person.
 | Risk Estimation and Evaluation
 | Degree of Possible Harm: |  |  | 25 | Possibility of Avoidance: |  |  | 2.5
 | Probability of Occurance of a Hazardous Event: |  |  | 0.05 | Frequency And/or Duration of Exposure: |  |  | 0.5
 | Pilz Hazard Rating (PHR): |  |  | 1.5625 | Summary Level: |  | Negligible Risk
 | Hazard Identification |  |  |  |  |  | Hazard No. | 1.3
 | Title | Fire Hazard
 | Location | Everywhere
 | Target | Entire body
 | Activity | Normal operation
 | Task | Driving
 | Sub Task | Both when charging and on idle state
 | Hazard Type | Burning
 | Sub Type | /
 | Description | Damaged batteries can cause the robot to catch fire during operation or charging.
 | References:
 | Risk Estimation and Evaluation
 | Degree of Possible Harm: |  |  | 1 | Possibility of Avoidance: |  |  | 0.75
 | Probability of Occurance of a Hazardous Event: |  |  | 1.25 | Frequency And/or Duration of Exposure: |  |  | 3
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

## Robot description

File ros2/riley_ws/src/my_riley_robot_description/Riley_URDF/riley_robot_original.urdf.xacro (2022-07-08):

<?xml version="1.0"?>
<robot name="riley_robot" xmlns:xacro="http://ros.org/wiki/xacro">
  <xacro:arg name="wheel_spacing_input" default="0.151" />
  <xacro:arg name="wheel_diameter_input" default="0.126" />
  <xacro:arg name="wheel_shaft_offset_input" default="0" />
  <xacro:arg name="rear_caster_offset_input" default="-0.200" />
  <xacro:arg name="back_wheel_diameter_input" default="0.06" />

  <xacro:property name="wheel_diameter" value="$(arg wheel_diameter_input)"/> 
  <xacro:property name="wheel_spacing" value="$(arg wheel_spacing_input)"/>
  <xacro:property name="wheel_shaft_offset" value="$(arg wheel_shaft_offset_input)"/>
  <xacro:property name="rear_caster_offset" value="$(arg rear_caster_offset_input)"/>
  <xacro:property name="back_wheel_diameter" value="$(arg back_wheel_diameter_input)"/>

  <link name="base_footprint"/>

  <link name="base_link"/>
  <joint name="base_link_joint" type="fixed">
    <origin xyz="0 0 ${wheel_diameter/2}" rpy="0 0 0" />
    <parent link="base_footprint"/>
    <child link="base_link" />
  </joint>

  <link name="chassis_link">
    <inertial>
      <origin xyz="0 0 0" rpy="0 0 0" />
      <mass value="0.317289185919371" />
      <inertia ixx="0.000970876188779837" ixy="6.94113413553014E-10" ixz="3.51219781695308E-06" iyy="0.00067590401119229" iyz="9.43089820999509E-10" izz="0.00152301084809347" />
    </inertial>
    <visual>
      <geometry>
        <box size="${-rear_caster_offset} ${wheel_spacing-0.05} 0.076"/> 
        <mesh filename="package://urdf_tutorial/STL_URDF/RILey_assembly-MiddlepartV1-1.STL"/>
      </geometry>
    </visual>
    <collision>
      <origin xyz="0 0 0.0" />
      <geometry>
        <box size="${-rear_caster_offset} ${wheel_spacing-0.05} 0.076"/>
        <mesh filename="package://urdf_tutorial/STL_URDF/RILey_assembly-MiddlepartV1-1.STL"/>
      </geometry>
    </collision>
  </link>
  
  <joint name="chassis_link_joint" type="fixed">
    <origin xyz="${rear_caster_offset/2} 0 0" rpy="0 0 0" />
    <parent link="base_link"/>
    <child link="chassis_link" />
  </joint>
  
  <xacro:macro name="wheel" params="prefix reflect">
    <link name="${prefix}_wheel">
      <visual>
        <origin xyz="${-wheel_diameter/2} ${-wheel_diameter/4} 0" rpy="${pi/2} 0 0"/>
        <geometry>
          <cylinder radius="${wheel_diameter/2}" length="0.044"/>
          <mesh filename="package://urdf_tutorial/STL_URDF/RILey_assembly-ReelyBuggyWheel_Right-2.STL"/>
        </geometry>
      </visual>
      <visual>
        <origin xyz="${-wheel_diameter/2} 0.01 0" rpy="${pi/2} 0 0"/>
        <geometry>
          <box size="${wheel_diameter/2} ${wheel_diameter/2} 0.02" />
        </geometry>
      </visual>
      <collision>
        <origin xyz="${-wheel_diameter/2} ${-wheel_diameter/4} 0" rpy="${pi/2} 0 0"/>
        <geometry>
          <cylinder radius="${wheel_diameter/2}" length="0.044"/>
        </geometry>
      </collision>
      <inertial>
        <origin xyz="0 0 0" rpy="0 0 0"/>
        <mass value="0.215732042845507"/>
        <inertia ixx="0.00025759718782391" ixy="2.12843584581061E-11" ixz="-5.66299342939977E-12" iyy="0.000452238839696424" iyz="3.99311464604179E-12" izz="0.000257597229543076" />
        </inertial>
    </link>
 
    
 
    <gazebo reference="${prefix}_wheel">
      <material>Gazebo/DarkGrey</material>
      <selfCollide>false</selfCollide>
      <mu1 value="1"/>
      <mu2 value="1"/>
      <kp value="10000000.0" />
      <kd value="1" />
      <fdir1 value="0 0 1"/>
    </gazebo>

    <joint name="${prefix}_wheel_joint" type="continuous">
      <axis xyz="0 ${-reflect} 0" rpy="0 0 0" />
      <parent link="base_link"/>
      <child link="${prefix}_wheel"/>
      <origin xyz="${wheel_shaft_offset} ${(0.5*wheel_spacing)*reflect} 0" rpy="${(reflect+1)*pi/2} 0 0"/>
    </joint>

    <transmission name="${prefix}_wheel_trans">
      <type>transmission_interface/SimpleTransmission</type>
      <joint name="${prefix}_wheel_joint">
        <hardwareInterface>hardware_interface/VelocityJointInterface</hardwareInterface>
      </joint>
      <actuator name="${prefix}_actuator">
        <mechanicalReduction>1</mechanicalReduction>
      </actuator>
    </transmission>
  </xacro:macro>

  <!-- add the wheels -->
  <xacro:wheel prefix="left" reflect="1"/>
  <xacro:wheel prefix="right" reflect="-1"/>
  
  <xacro:macro name="sphere_inertia" params="m r">
    <inertial>
      <mass value="${m}"/>
      <inertia ixx="${2.0*m*(r*r)/5.0}" ixy="0.0" ixz="0.0" iyy="${2.0*m*(r*r)/5.0}" iyz="0.0" izz="${2.0*m*(r*r)/5.0}"/>
    </inertial>
  </xacro:macro>
  
  <link name="back_wheel">
    <visual>
      <origin rpy="1.57075 0 0" xyz="0 0 0"/>
      <geometry>
        <sphere radius="${back_wheel_diameter/2}"/>
        <mesh filename="package://urdf_tutorial/STL_URDF/RILey_assembly-Backwheel-1.STL"/>
      </geometry>
    </visual>
    <collision>
      <origin xyz="0 0 0" rpy="1.57075 0 0"/>
      <geometry>
        <sphere radius="${back_wheel_diameter/2}"/>
        <mesh filename="package://urdf_tutorial/STL_URDF/RILey_assembly-Backwheel-1.STL"/>
      </geometry>
    </collision>
    <xacro:sphere_inertia m="0.1" r="${back_wheel_diameter/2}"/>
  </link>
  
  <joint name="back_wheel_joint" type="continuous">
    <axis xyz="-0.133333333333 0 -0.015" rpy="0 0 0" />
    <origin xyz="${rear_caster_offset} 0 ${-back_wheel_diameter/2}" rpy="0 0 0"/>
    <parent link="chassis_link"/>
    <child link="back_wheel"/>
  </joint>

  <gazebo reference="back_wheel">
    <material>Gazebo/DarkGrey</material>
    <selfCollide>false</selfCollide>
    <mu1 value="0.05"/>
    <mu2 value="0.05"/>
    <kp value="10000000.0" />
    <kd value="1" />
    <fdir1 value="0 0 1"/>
  </gazebo>

  <gazebo>
    <plugin name="gazebo_ros_control" filename="libgazebo_ros_control.so">
      <robotNamespace></robotNamespace>
    </plugin>

    <plugin name="p3d_base_controller" filename="libgazebo_ros_p3d.so">
      <alwaysOn>true</alwaysOn>
      <updateRate>50.0</updateRate>
      <bodyName>base_footprint</bodyName>
      <topicName>pose_ground_truth</topicName>
      <gaussianNoise>0.01</gaussianNoise>
      <frameName>map</frameName>
      <xyzOffsets>0 0 0</xyzOffsets>
      <rpyOffsets>0 0 0</rpyOffsets>
    </plugin>
  </gazebo>

  <gazebo reference="base_link">
    <turnGravityOff>false</turnGravityOff>
  </gazebo>
  <gazebo reference="chassis_link">
    <turnGravityOff>false</turnGravityOff>
  </gazebo>
  
  

</robot>

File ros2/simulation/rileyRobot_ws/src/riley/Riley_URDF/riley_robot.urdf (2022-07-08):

<?xml version="1.0"?>
<robot name="riley_robot">
  <material name="grey">
      <color rgba="0.5 0.5 0.5 1.0" />
  </material>
  
  
  <link name="base_link">
    <visual>
      <origin xyz="0 0 0" rpy="0 0 0" />
      <geometry>
        <mesh filename="package://riley/models/riley/meshes/MiddlepartV2.STL"/>
      </geometry>
      <material name="grey"/>
    </visual>
  </link>
  
  <link name="tail_link">
    <visual>
      <origin xyz="0 0 0" rpy="0 0 0" />
      <geometry> 
        <mesh filename="package://riley/models/riley/meshes/MiddlepartTailV2.STL"/>
      </geometry>
      <material name="grey"/>
    </visual>
  </link>
  
  <joint name="tail_link_joint" type="fixed">
    <origin xyz="-0.093 0.0 -0.0115" rpy="0 0 0" />
    <parent link="base_link"/>
    <child link="tail_link" />
  </joint>

  <link name="left_wheel">
      <visual>
        <origin xyz="0 0 0" rpy="0 0 0" />
        <geometry>
          <mesh filename="package://riley/models/riley/meshes/ReelyBuggyWheel_Left.STL"/>
        </geometry>
        <material name="grey"/>
      </visual>
  </link>
    
  <link name="right_wheel">
      <visual>
        <origin xyz="0 0 0" rpy="0 0 0" />
        <geometry>
          <mesh filename="package://riley/models/riley/meshes/ReelyBuggyWheel_Right.STL"/>
        </geometry>
        <material name="grey"/>
      </visual>
  </link>
    
  <joint name="left_wheel_joint" type="continuous">
      <axis xyz="0 1 0" />
      <parent link="base_link"/>
      <child link="left_wheel"/>
      <origin xyz="0 0.14 -0.01575" rpy="-1.57 0 0"/>
  </joint>
    
  <joint name="right_wheel_joint" type="continuous">
      <axis xyz="0 1 0" />
      <parent link="base_link"/>
      <child link="right_wheel"/>
      <origin xyz="0 -0.14 -0.01575" rpy="-1.57 0 0"/>
  </joint>
  
  <link name="back_wheel">
    <visual>
      <origin xyz="0 0 0" rpy="0 0 0" />
      <geometry>
        <sphere radius="0.03"/>
        <mesh filename="package://riley/models/meshes/SwivelWheel-SwivelWheelWheel-1.STL"/>
      </geometry>
      <material name="grey"/>
    </visual>
  </link>
  
  <joint name="back_wheel_joint" type="fixed">
    <parent link="tail_link"/>
    <child link="back_wheel"/>
    <origin xyz="-0.04 0.0 -0.039" rpy="0 0 0"/>
  </joint>
    

  <link name="imu_link">
    <visual>
      <origin xyz="0 0 0" rpy="0 0 0" />
      <geometry>
        <mesh filename="package://riley/models/riley/meshes/RILey_assembly-PCB-1MPU9250.STEP-1V1.STEP-1.STL"/>
      </geometry>
    </visual>
  </link>

  <joint name="imu_joint" type="fixed">
    <parent link="base_link"/>
    <child link="imu_link"/>
    <origin xyz="0 0.01 0"/>
  </joint>

  
  <link name="lidar_link">
    <visual>
      <origin xyz="0 0 0" rpy="0 0 0"/>
      <geometry>
         <mesh filename="package://riley/models/riley/meshes/RILey_assembly%20-%20LD06_Assembly-1%20LD06_LiDAR-1%20LD06_LiDAR-1.STL"/>
      </geometry>
    </visual>
  </link>
    
  <joint name="lidar_joint" type="fixed">
    <parent link="base_link"/>
    <child link="lidar_link"/>
    <origin xyz="0 0 0.054" rpy="0 0 0"/>
  </joint>
  
  
  <link name="camera_link">
    <visual>
      <origin xyz="0 0 0" rpy="0 0 0"/>
      <geometry>
        <mesh filename="package://riley/models/riley/meshes/RILey_assembly-Cam V2.1 v1.step-1.STL"/>
      </geometry>
    </visual>
  </link>

  
  <joint name="camera_joint" type="fixed">
    <parent link="base_link"/>
    <child link="camera_link"/>
    <origin xyz="0.045 0 0.03" rpy="0 0 0"/>
  </joint>

  <link name="camera_depth_frame"/>

  <joint name="camera_depth_joint" type="fixed">
    <origin xyz="0 0 0" rpy="-1.57 0 -1.57"/>
    <parent link="camera_link"/>
    <child link="camera_depth_frame"/>
  </joint>

</robot>

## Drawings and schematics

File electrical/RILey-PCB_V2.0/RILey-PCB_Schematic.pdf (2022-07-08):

17-6-2022 14:00 C:\Users\Quinv\AppData\Local\Temp\Neutron\ElectronFileOutput\7320\sch-88676faa-6dc8-41e5-9c08-79e2eb314ad8\RILey PCB V2.0 v56.sch (Sheet: 1/1) ⁺¹²V | +5V

# 5 C¹

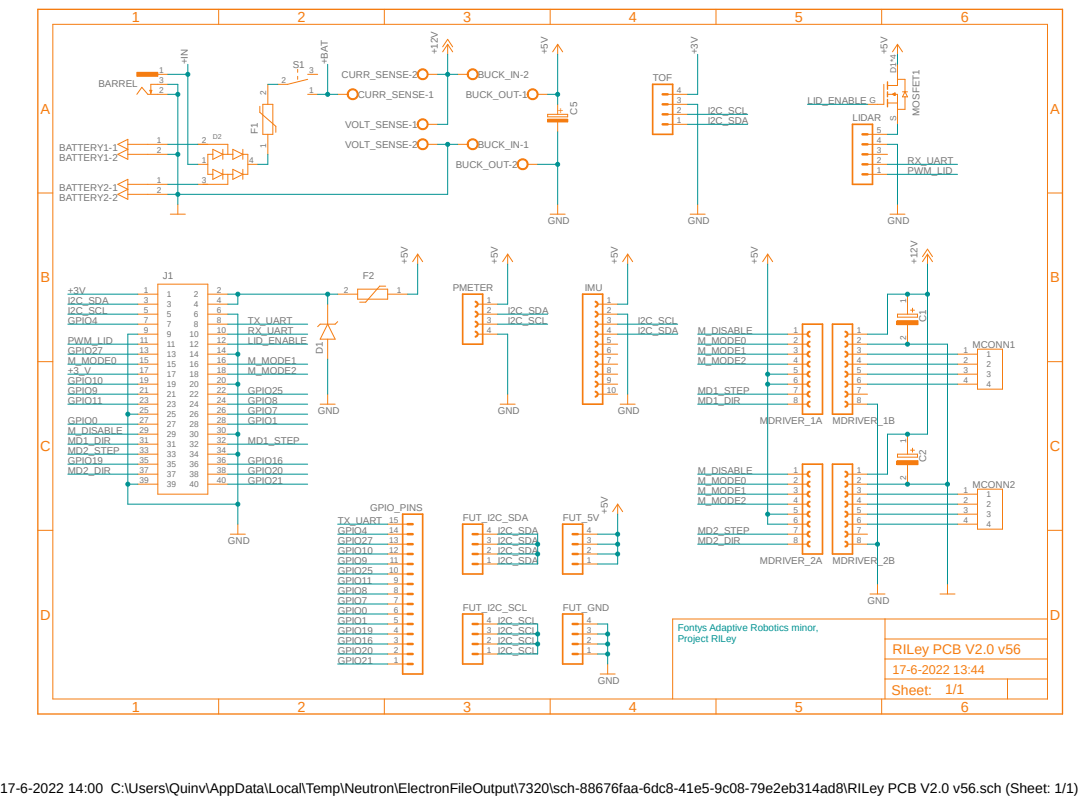
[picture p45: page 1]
GND +5V; GND ⁺⁵V; GND; GND⁺⁵V; BATTERY1-1; 1 BATTERY1-2 2 BUCK_IN-1; BUCK_IN-2; BUCK_OUT-1; BUCK_OUT-2; MDRIVER_1A; 1 2 3 4 5 6 7 8 MDRIVER_1B; 1 2 3 4 5 6 7 8 MDRIVER_2A; 1 2 3 4 5 6 7 8 MDRIVER_2B; MCONN1 1; 4 MCONN2; BARREL; 3 CURR_SENSE-1; CURR_SENSE-2; VOLT_SENSE-1; VOLT_SENSE-2; IMU; 10 PMETER 1 2 3 4; LIDAR; FUT_I2C_SCL; 4 FUT_I2C_SDA; 4 FUT_GND; 4 FUT_5V; BATTERY2-1; 1 BATTERY2-2; 2 TOF; MOSFET1 G; GPIO_PINS; RX_UART; TX_UART; M_MODE0; MD2_DIR; MD2_STEP; MD1_DIR; MD1_STEP; GPIO19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

Fontys Adaptive Robotics minor, Project RILey

Sheet: 1/1

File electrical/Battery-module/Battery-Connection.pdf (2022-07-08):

SpiceOrder 1 | SpiceOrder 2 SpiceOrder 1 | SpiceOrder 2 SpiceOrder 2 | SpiceOrder 1 SpiceOrder 2 | SpiceOrder 1 | GND

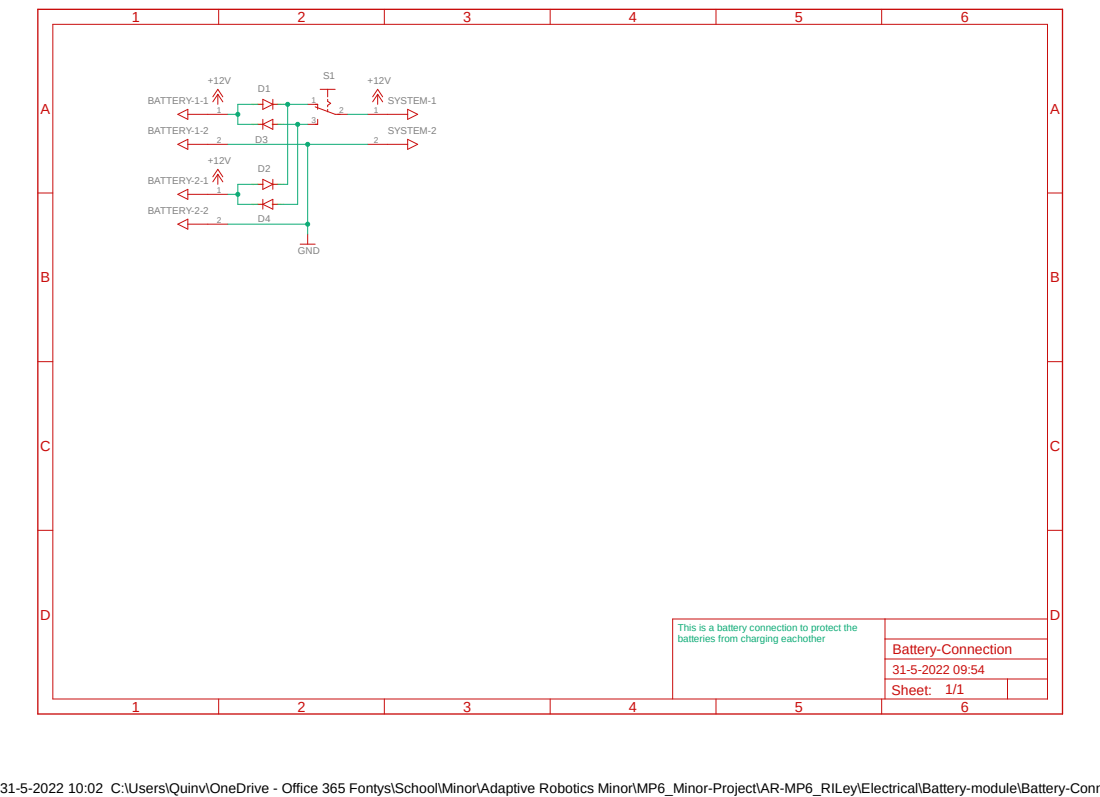
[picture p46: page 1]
1 BATTERY-1-1; 2 BATTERY-1-2; 1 BATTERY-2-1; 2 BATTERY-2-2; 1 SYSTEM-1; 2 SYSTEM-2; Battery-Connection

This is a battery connection to protect the batteries from charging eachother

Sheet: 1/1

31-5-2022 10:02 C:\Users\Quinv\OneDrive - Office 365 Fontys\School\Minor\Adaptive Robotics Minor\MP6_Minor-Project\AR-MP6_RILey\Electrical\Battery-module\Battery-Connection.sch (Sheet: 1/1)

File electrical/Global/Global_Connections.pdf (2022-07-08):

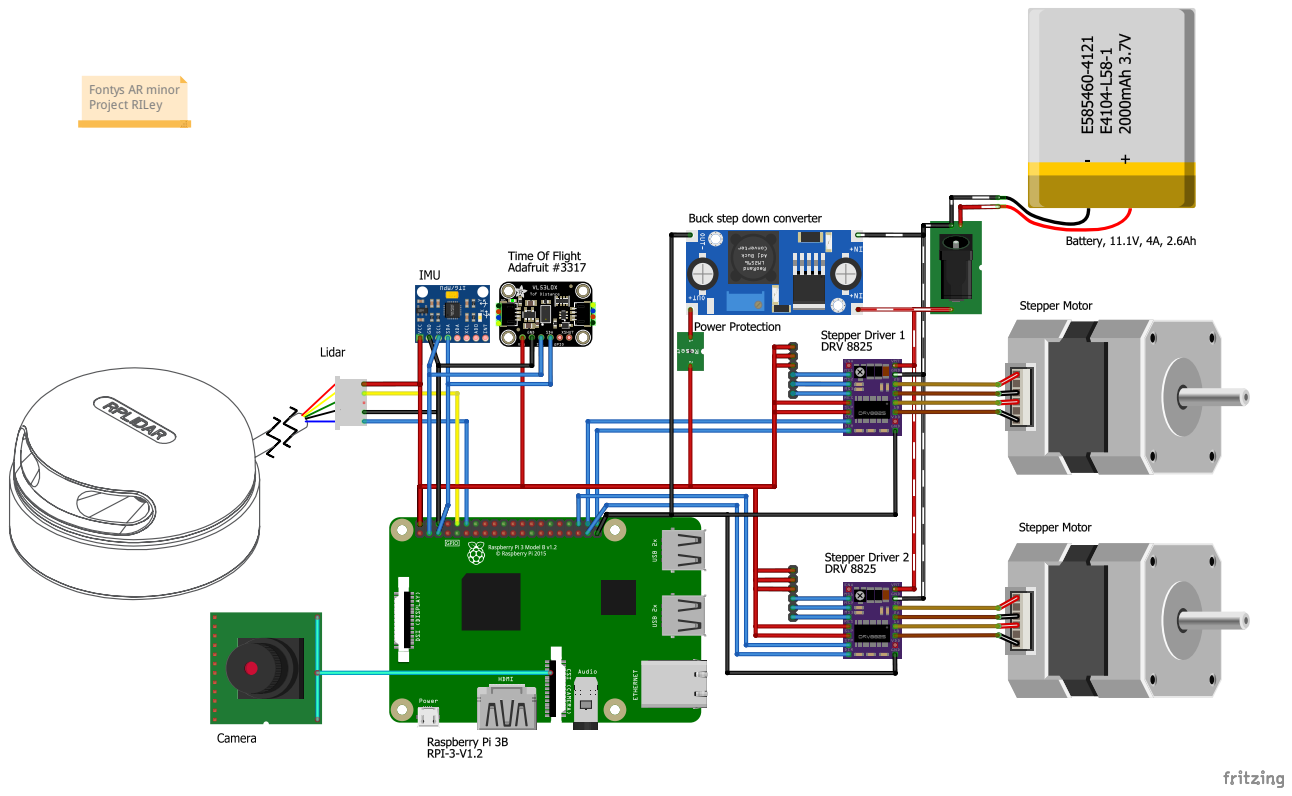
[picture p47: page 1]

Fontys AR minor
Project RILey

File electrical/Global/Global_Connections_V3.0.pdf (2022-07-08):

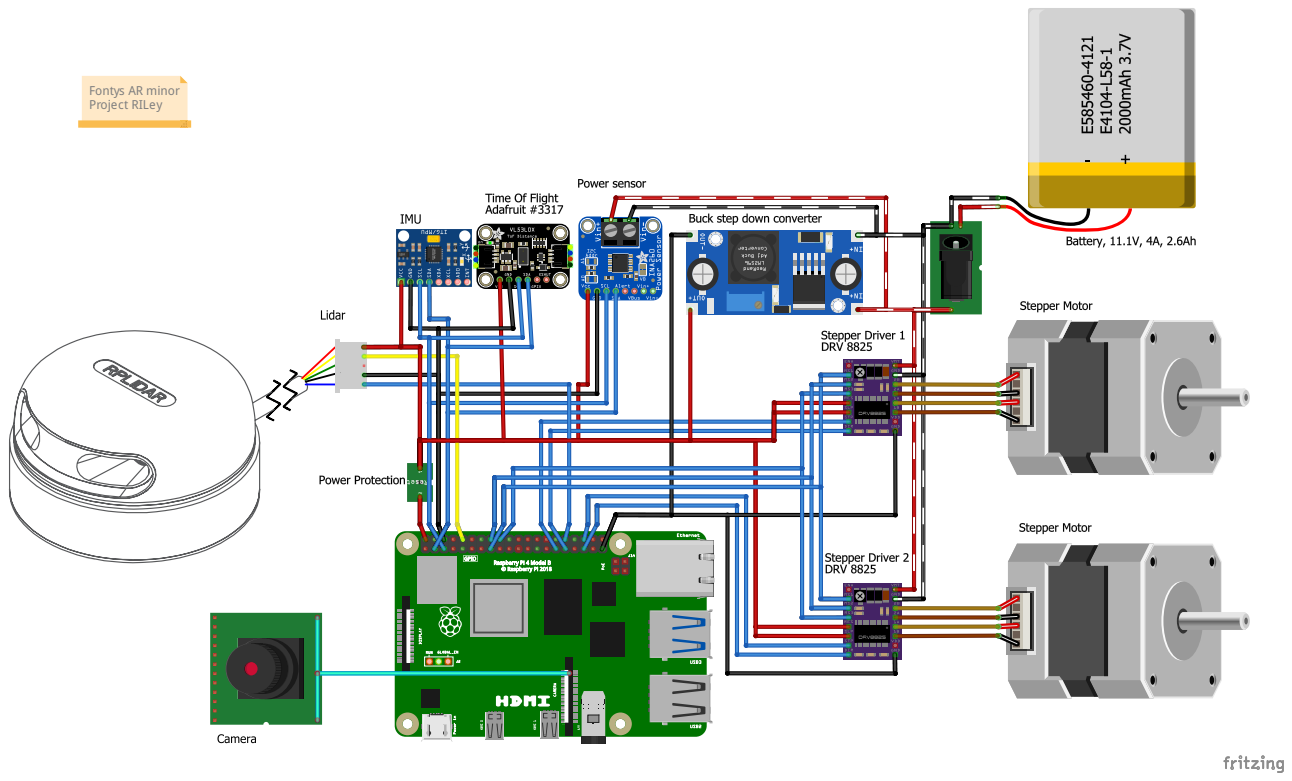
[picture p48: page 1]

Fontys AR minor
Project RILey

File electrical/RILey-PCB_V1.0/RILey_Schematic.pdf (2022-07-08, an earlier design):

A

A

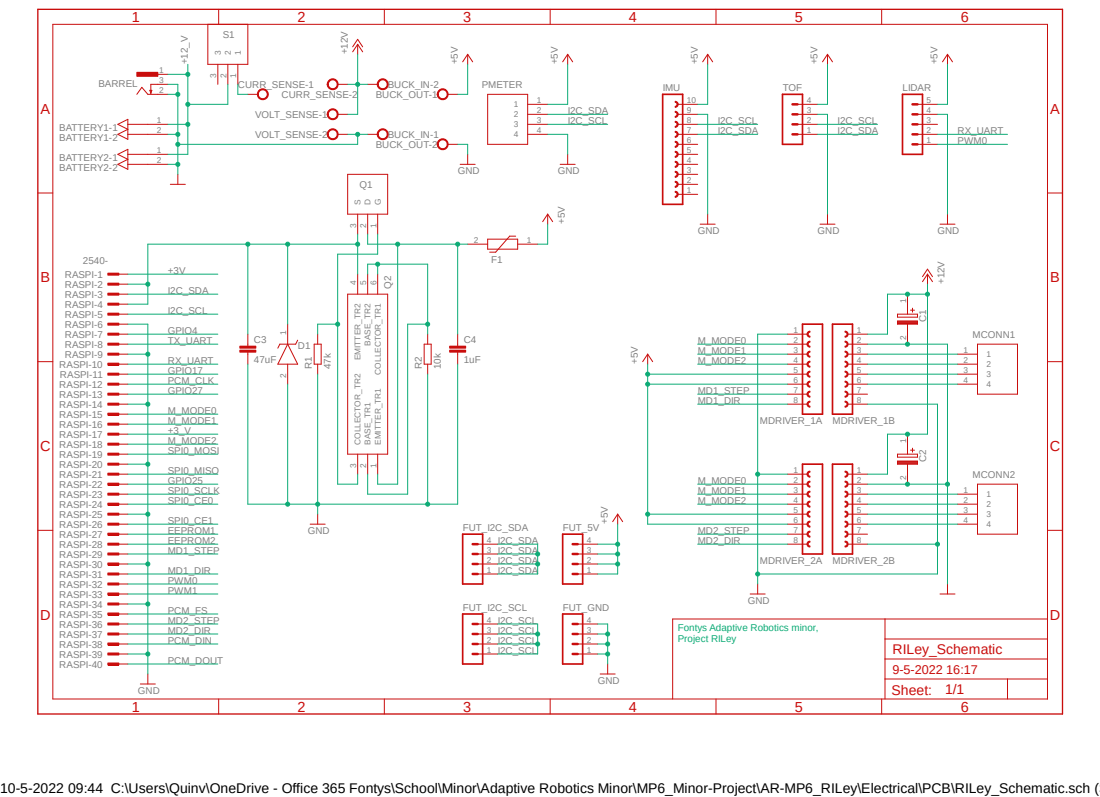
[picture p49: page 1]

Fontys Adaptive Robotics minor, Project RILey

Sheet: 1/1

10-5-2022 09:44 C:\Users\Quinv\OneDrive - Office 365 Fontys\School\Minor\Adaptive Robotics Minor\MP6_Minor-Project\AR-MP6_RILey\Electrical\PCB\RILey_Schematic.sch (Sheet: 1/1)

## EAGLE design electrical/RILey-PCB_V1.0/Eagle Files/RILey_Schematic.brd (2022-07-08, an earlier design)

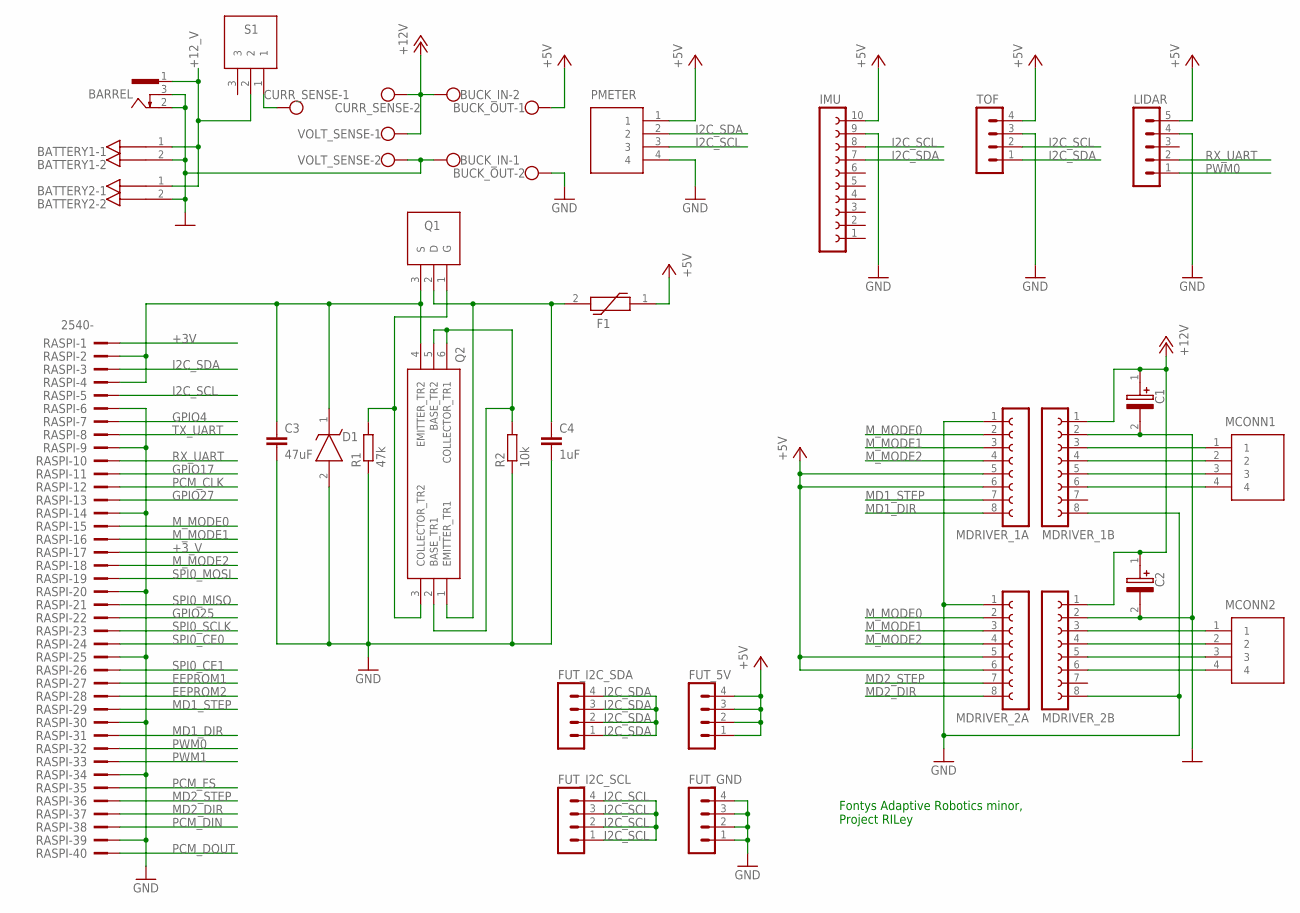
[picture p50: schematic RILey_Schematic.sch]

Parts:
BARREL: 733980-62
BATTERY1, BATTERY2: 0026604020; KK41791-4020_2-PIN
BUCK_IN: W237-102
BUCK_OUT: W237-102
C1, C2: 100uF; CAPPRD250W50D655H1250
C3: 47uF; C5B2.5
C4: 1uF; C2.5-3
CURR_SENSE: W237-102
D1: SA5.0A-E3_54; DIOAD1910W86L670D310
F1: PTS18126V260; FUSC4632X90N
FUT_5V: MA04-1
FUT_GND: MA04-1
FUT_I2C_SCL, FUT_I2C_SDA: MA04-1
IMU: FE10-1; FE10
LIDAR: MA05-1
MCONN1, MCONN2: B4B-XH-A_LF__SN_; SHDR4W64P0X250_1X4_1240X575X70
MDRIVER_1A, MDRIVER_1B, MDRIVER_2A, MDRIVER_2B: FE08-1; FE08
PMETER: BLG1X4; RHDR4W64P0X254_1X4_1066X250X86
Q1: IRF9530NPBF; TO254P469X1042X1967-3P
Q2: BCM857BS,115; SOT65P210X110-6N
R1: 47k; 0207/10
R2: 10k; 0207/10
RASPI: 2540-; PAK100/2500-40
S1: 1101M2S3CQE2; 1000-SERIES(SPDT)
TOF: MA04-1
VOLT_SENSE: W237-102

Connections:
0V: BARREL.2, BARREL.3, BATTERY1.2, BATTERY2.2, BUCK_IN.1, C1.2 (-), C2.2 (-), MDRIVER_1B.2, MDRIVER_2B.2, VOLT_SENSE.2
+3V: RASPI.1
+3_V: RASPI.17
+5V: BUCK_OUT.1, F1.1, FUT_5V.1, FUT_5V.2, FUT_5V.3, FUT_5V.4, IMU.10, LIDAR.5, MDRIVER_1A.5, MDRIVER_1A.6, MDRIVER_2A.5, MDRIVER_2A.6, PMETER.1, TOF.4
+12V: BUCK_IN.2, C1.1 (+), C2.1 (+), CURR_SENSE.2, MDRIVER_1B.1, MDRIVER_2B.1, VOLT_SENSE.1
+12_V: BARREL.1, BATTERY1.1, BATTERY2.1, S1.2
EEPROM1: RASPI.27
EEPROM2: RASPI.28
GND: BUCK_OUT.2, C3.2, C4.2, D1.2 (A), FUT_GND.1, FUT_GND.2, FUT_GND.3, FUT_GND.4, IMU.9, LIDAR.4, MDRIVER_1A.1, MDRIVER_1B.8, MDRIVER_2A.1, MDRIVER_2B.8, PMETER.4, R1.1, R2.1, RASPI.6, RASPI.9, RASPI.14, RASPI.20, RASPI.25, RASPI.30, RASPI.34, RASPI.39, TOF.3
GPIO4: RASPI.7
GPIO17: RASPI.11
GPIO25: RASPI.22
GPIO27: RASPI.13
I2C_SCL: FUT_I2C_SCL.1, FUT_I2C_SCL.2, FUT_I2C_SCL.3, FUT_I2C_SCL.4, IMU.8, PMETER.3, RASPI.5, TOF.2
I2C_SDA: FUT_I2C_SDA.1, FUT_I2C_SDA.2, FUT_I2C_SDA.3, FUT_I2C_SDA.4, IMU.7, PMETER.2, RASPI.3, TOF.1
MD1_DIR: MDRIVER_1A.8, RASPI.31
MD1_STEP: MDRIVER_1A.7, RASPI.29
MD2_DIR: MDRIVER_2A.8, RASPI.37
MD2_STEP: MDRIVER_2A.7, RASPI.36
M_MODE0: MDRIVER_1A.2, MDRIVER_2A.2, RASPI.15
M_MODE1: MDRIVER_1A.3, MDRIVER_2A.3, RASPI.16
M_MODE2: MDRIVER_1A.4, MDRIVER_2A.4, RASPI.18
unnamed: MCONN1.1, MDRIVER_1B.3
unnamed: MCONN1.2, MDRIVER_1B.4
unnamed: MCONN1.3, MDRIVER_1B.5
unnamed: MCONN1.4, MDRIVER_1B.6
unnamed: MCONN2.1, MDRIVER_2B.3
unnamed: MCONN2.2, MDRIVER_2B.4
unnamed: MCONN2.3, MDRIVER_2B.5
unnamed: MCONN2.4, MDRIVER_2B.6
unnamed: Q1.1 (G), Q2.3 (COLLECTOR_TR2), R1.2
unnamed: CURR_SENSE.1, S1.1
unnamed: C4.1, F1.2, Q1.2 (D), Q2.1 (EMITTER_TR1)
unnamed: C3.1, D1.1 (K), Q1.3 (S), Q2.4 (EMITTER_TR2), RASPI.2, RASPI.4
unnamed: Q2.2 (BASE_TR1), Q2.5 (BASE_TR2), Q2.6 (COLLECTOR_TR1), R2.2
PCM_CLK: RASPI.12
PCM_DIN: RASPI.38
PCM_DOUT: RASPI.40
PCM_FS: RASPI.35
PWM0: LIDAR.1, RASPI.32
PWM1: RASPI.33
RX_UART: LIDAR.2, RASPI.10
SPI0_CE0: RASPI.24
SPI0_CE1: RASPI.26
SPI0_MISO: RASPI.21
SPI0_MOSI: RASPI.19
SPI0_SCLK: RASPI.23
TX_UART: RASPI.8

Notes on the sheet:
Fontys Adaptive Robotics minor, Project RILey

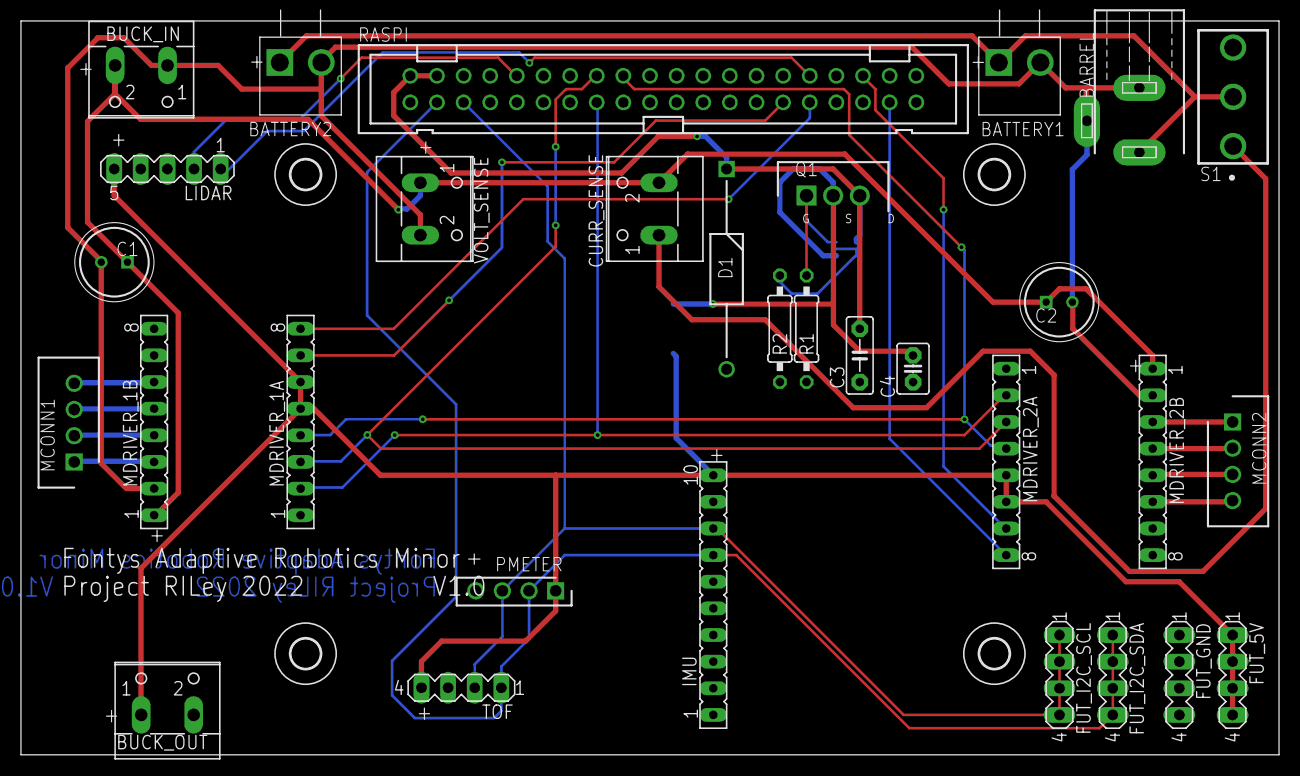
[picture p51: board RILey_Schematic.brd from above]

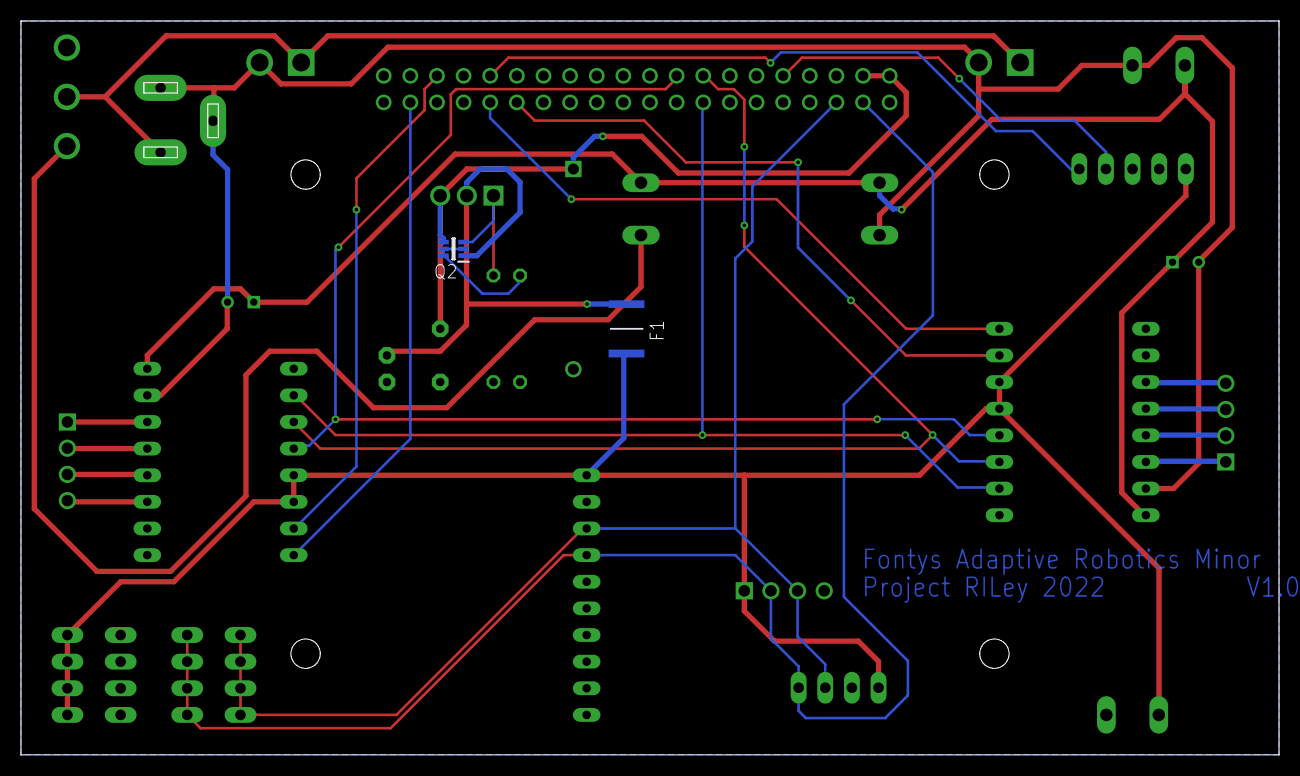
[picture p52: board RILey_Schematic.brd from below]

Board: 2 copper layers, 120.0 x 70.0 mm, 37 parts (2 on the bottom side), 29 nets.

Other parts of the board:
U$1, U$3, U$4, U$5: 2,8

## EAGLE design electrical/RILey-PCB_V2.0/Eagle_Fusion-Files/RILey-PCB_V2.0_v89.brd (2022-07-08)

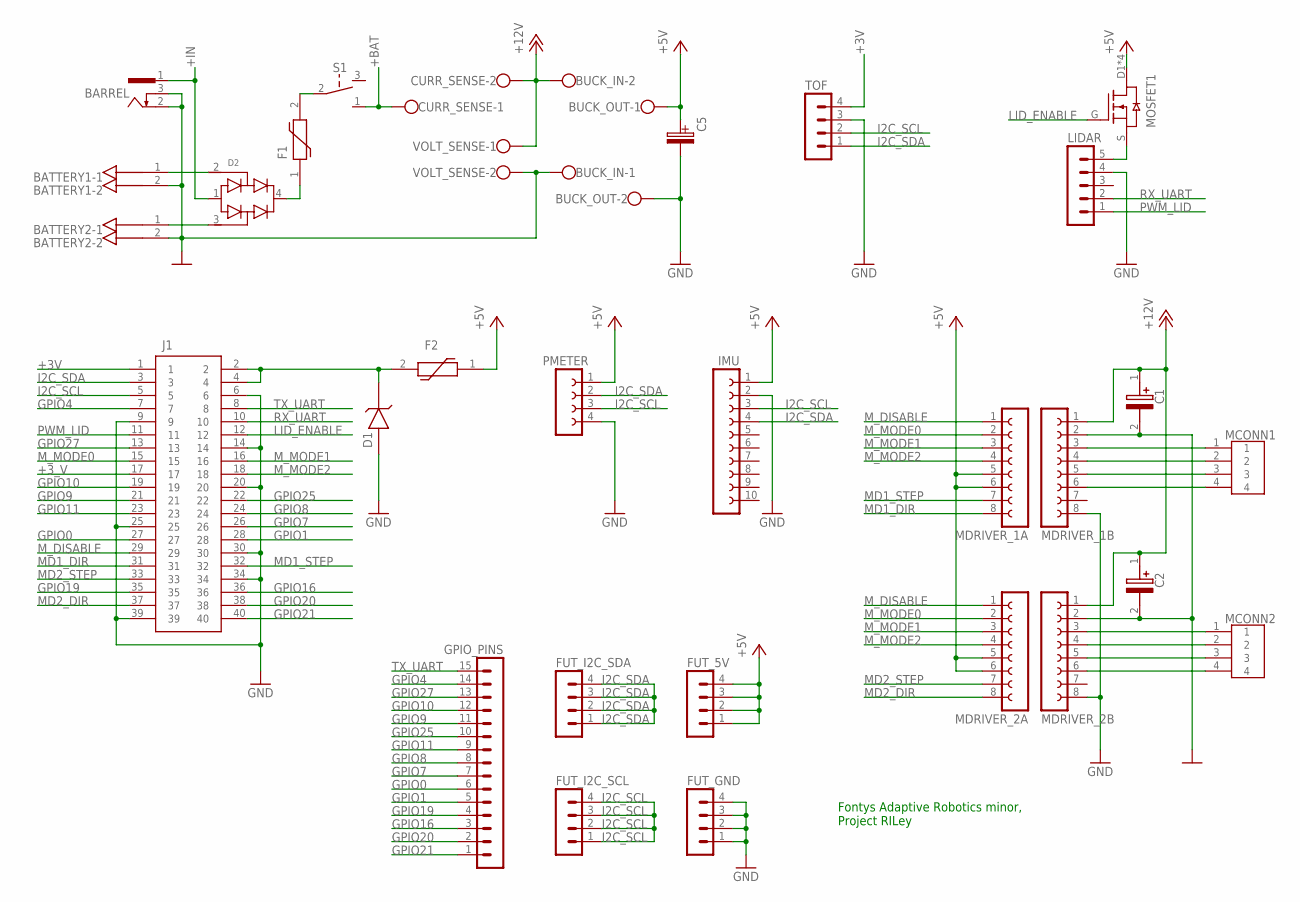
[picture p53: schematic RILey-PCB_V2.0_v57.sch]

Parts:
BARREL: DC_BARREL0-62; 733980-62
BATTERY1, BATTERY2: 0026604020; KK41791-4020_2-PIN
BUCK_IN: W237-102
BUCK_OUT: W237-102
C1, C2: 100uF; CAPPRD250W50D655H1250
C5: ELECTROLYTIC_CAPACITOR'8*20'; ELECTROLYTIC_CAPACITOR
CURR_SENSE: W237-102
D1: ZENER-THDO-35; ZENER-TH
D2: DIODE-BRIGDE; DIODE-BRIDGE
F1: 2920L400/15MR
F2: 1812L300MR
FUT_5V: MA04-1_SMALLPAD; MA04-1_S
FUT_GND: MA04-1_SMALLPAD; MA04-1_S
FUT_I2C_SCL, FUT_I2C_SDA: MA04-1_SMALLPAD; MA04-1_S
GPIO_PINS: MA15-1W
IMU: FE10-1_3D; FE10-1
J1: MC-254-40-00-ST-DIP
LIDAR: MA05-1_SMALLPAD; MA05-1_S
MCONN1, MCONN2: B4B-XH-A_LF__SN_
MDRIVER_1A, MDRIVER_1B, MDRIVER_2A, MDRIVER_2B: FE08-1_3D; FE08-1
MOSFET1: SI2303CDS-T1-GE3; TSOP6_SOT457
PMETER: FE04-1
S1: 1101M2S3CQE2; 1000-SERIES(SPDT)
TOF: MA04-1W
VOLT_SENSE: W237-102

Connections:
0V: BARREL.2, BARREL.3, BATTERY1.2, BATTERY2.2, BUCK_IN.1, C1.2 (-), C2.2 (-), MDRIVER_1B.2, MDRIVER_2B.2, VOLT_SENSE.2
+3V: J1.1, TOF.4
+3_V: J1.17
+5V: BUCK_OUT.1, C5.+, F2.1, FUT_5V.1, FUT_5V.2, FUT_5V.3, FUT_5V.4, IMU.1, MDRIVER_1A.5, MDRIVER_1A.6, MDRIVER_2A.5, MDRIVER_2A.6, MOSFET1.D1 (D), MOSFET1.D2 (D), MOSFET1.D3 (D), MOSFET1.D4 (D), PMETER.1
+5V_FUSED: D1.C, F2.2, J1.2, J1.4
+12V: BUCK_IN.2, C1.1 (+), C2.1 (+), CURR_SENSE.2, MDRIVER_1B.1, MDRIVER_2B.1, VOLT_SENSE.1
+BAT: CURR_SENSE.1, S1.1
+BAT1: BATTERY1.1, D2.2
+BAT2: BATTERY2.1, D2.3
+IN: BARREL.1, D2.1
GND: BUCK_OUT.2, C5.-, D1.A, FUT_GND.1, FUT_GND.2, FUT_GND.3, FUT_GND.4, IMU.2, J1.6, J1.9, J1.14, J1.20, J1.25, J1.30, J1.34, J1.39, LIDAR.4, MDRIVER_1B.8, MDRIVER_2B.8, PMETER.4, TOF.3
GPIO0: GPIO_PINS.6, J1.27
GPIO1: GPIO_PINS.5, J1.28
GPIO4: GPIO_PINS.14, J1.7
GPIO7: GPIO_PINS.7, J1.26
GPIO8: GPIO_PINS.8, J1.24
GPIO9: GPIO_PINS.11, J1.21
GPIO10: GPIO_PINS.12, J1.19
GPIO11: GPIO_PINS.9, J1.23
GPIO16: GPIO_PINS.3, J1.36
GPIO19: GPIO_PINS.4, J1.35
GPIO20: GPIO_PINS.2, J1.38
GPIO21: GPIO_PINS.1, J1.40
GPIO25: GPIO_PINS.10, J1.22
GPIO27: GPIO_PINS.13, J1.13
I2C_SCL: FUT_I2C_SCL.1, FUT_I2C_SCL.2, FUT_I2C_SCL.3, FUT_I2C_SCL.4, IMU.3, J1.5, PMETER.3, TOF.2
I2C_SDA: FUT_I2C_SDA.1, FUT_I2C_SDA.2, FUT_I2C_SDA.3, FUT_I2C_SDA.4, IMU.4, J1.3, PMETER.2, TOF.1
IN: D2.4, F1.1
LID_ENABLE: J1.12, MOSFET1.G
MD1_DIR: J1.31, MDRIVER_1A.8
MD1_STEP: J1.32, MDRIVER_1A.7
MD2_DIR: J1.37, MDRIVER_2A.8
MD2_STEP: J1.33, MDRIVER_2A.7
M_DISABLE: J1.29, MDRIVER_1A.1, MDRIVER_2A.1
M_MODE0: J1.15, MDRIVER_1A.2, MDRIVER_2A.2
M_MODE1: J1.16, MDRIVER_1A.3, MDRIVER_2A.3
M_MODE2: J1.18, MDRIVER_1A.4, MDRIVER_2A.4
unnamed: LIDAR.5, MOSFET1.S
unnamed: F1.2, S1.2
unnamed: MCONN1.1, MDRIVER_1B.3
unnamed: MCONN1.2, MDRIVER_1B.4
unnamed: MCONN1.3, MDRIVER_1B.5
unnamed: MCONN1.4, MDRIVER_1B.6
unnamed: MCONN2.1, MDRIVER_2B.3
unnamed: MCONN2.2, MDRIVER_2B.4
unnamed: MCONN2.3, MDRIVER_2B.5
unnamed: MCONN2.4, MDRIVER_2B.6
PWM_LID: J1.11, LIDAR.1
RX_UART: J1.10, LIDAR.2
TX_UART: GPIO_PINS.15, J1.8

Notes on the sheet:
Fontys Adaptive Robotics minor, Project RILey

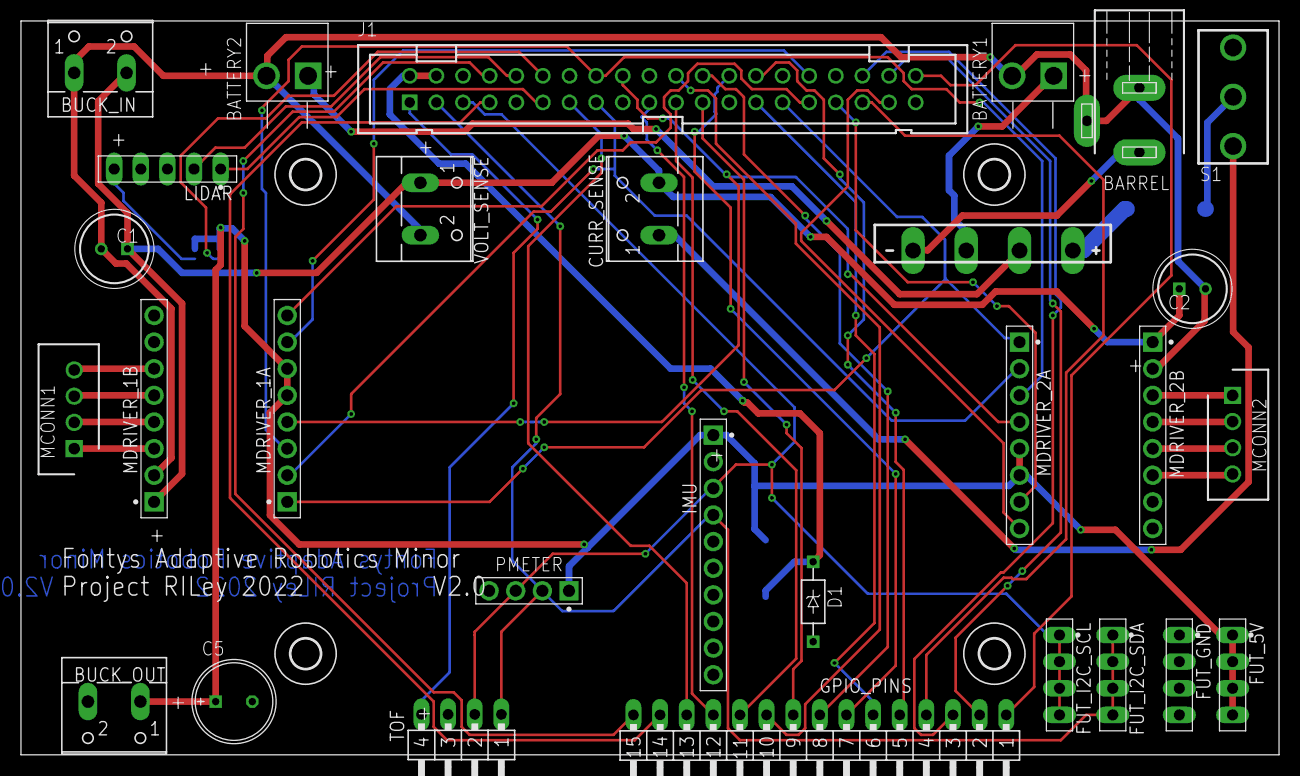
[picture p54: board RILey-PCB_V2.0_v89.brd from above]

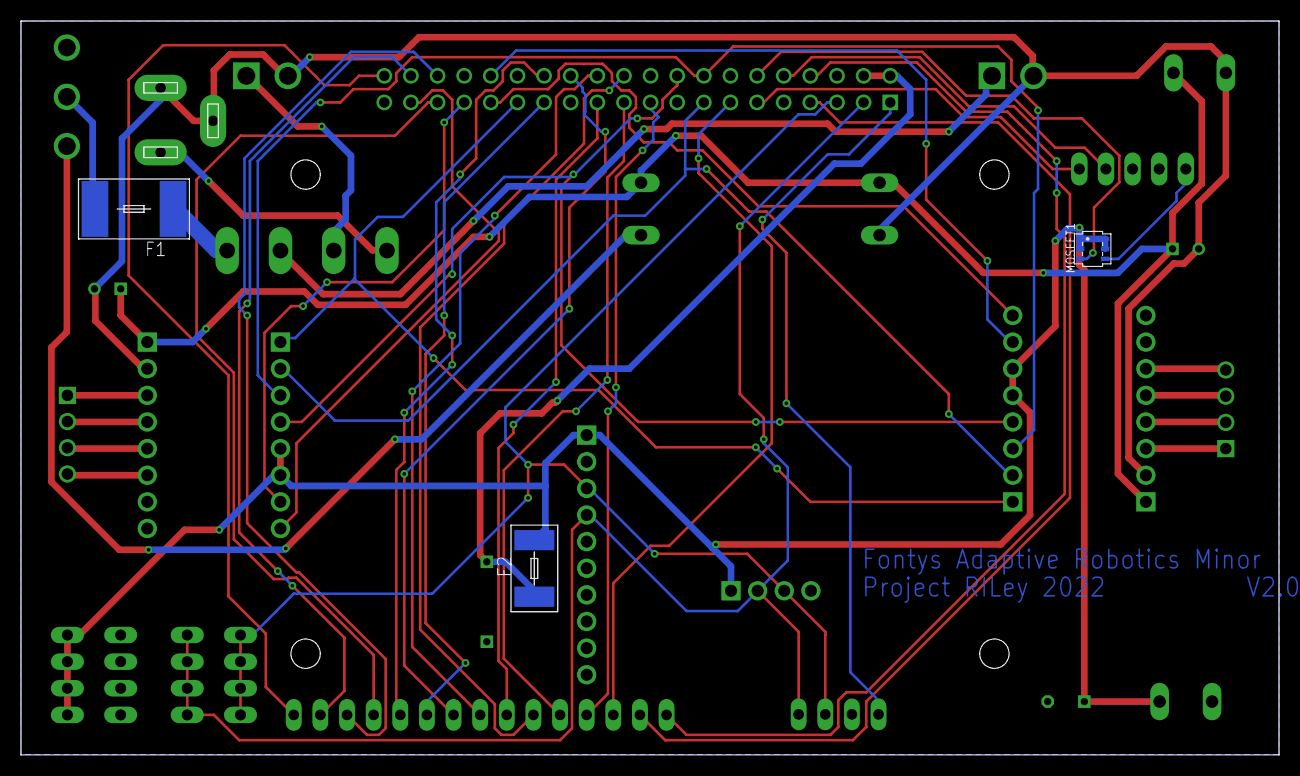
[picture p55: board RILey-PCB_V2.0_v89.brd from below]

Board: 2 copper layers, 120.0 x 70.0 mm, 36 parts (3 on the bottom side), 49 nets.

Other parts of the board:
U$1, U$3, U$4, U$5: 2,8

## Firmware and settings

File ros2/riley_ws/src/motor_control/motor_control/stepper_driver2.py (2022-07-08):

import time
from threading import Thread
from time import sleep

import rclpy
import RPi.GPIO as GPIO
from rclpy.callback_groups import MutuallyExclusiveCallbackGroup
from rclpy.executors import MultiThreadedExecutor
from rclpy.node import Node
from riley_interfaces.msg import IMUSensor, TOFSensor, XboxInput

from motor_control.pid import PID


class stepperMotorDriver(Node):
    def __init__(self):
        super().__init__('Stepper_Driver_2')
        # Multithreading settings
        self.group1 = MutuallyExclusiveCallbackGroup()
        self.group2 = MutuallyExclusiveCallbackGroup()
        self.group3 = MutuallyExclusiveCallbackGroup()
        
        self.get_logger().info('Creating a subscriber to xbox controller now')
        self.subscription = self.create_subscription(XboxInput, 'xbox_input', self.controller_callback, 10, callback_group=self.group1)
        
        self.get_logger().info('Creating a subscriber to IMU sensor data now')
        self.subscriptionIMU = self.create_subscription(IMUSensor, 'imu_sensor', self.IMU, 10, callback_group=self.group2)
        
        self.get_logger().info('Creating a subscriber to TOF sensor data now')
        self.subscriptionTOF = self.create_subscription(TOFSensor, 'tof_sensor', self.TOF, 10, callback_group=self.group3)  
                
        # GPIO pins used
        self.StepperEnable = 5                  # Enable pin of the motors
        self.StepperRightDIR = 6                # Direction of motor 1
        self.StepperRightSTEP = 12              # Step of motor 1
        self.StepperLeftDIR = 26                # Direction of motor 2
        self.StepperLeftSTEP = 13               # Step of motor 2
        self.MODE = (22, 23, 24)                # Microstep Resolution GPIO Pins
        
        # Variables
        self.CW = 0                             # Clockwise Rotation
        self.CCW = 1                            # Counterclockwise Rotation
        self.SPR = 1                            # Steps per Revolution (360 / 7.5)
        self.startup_right = 0.1                # Starting speed
        self.startup_left = 0.1                 # Starting speed
        self.kp = 0.25                          # Proportional gain
        self.vel_limits = (0, 10.0)             # Speed limits
        self.delay_limits = (0.0003, 0.005)     # "Delay" limits where delay is time to wait (not using delays)
        self.speed_delay_left = 1               # The actual "delay" the motors are stepping in
        self.speed_delay_right = 1              # The actual "delay" the motors are stepping in
        
        self.print_flag = 0                     # Debug print cap flag
        
        self.flipping_time = 0                  # Last time flip was detected
        self.gap_time = 0                       # Last time a gap was detected
        self.obs_time = 0                       # Last time an obstacle was detected
        
        self.l_dir = self.CCW
        self.r_dir = self.CW
        self.right_wheel = PID(kp=self.kp, updateTime=0)
        self.left_wheel = PID(kp=self.kp, updateTime=0)
        self.result_right = 0
        self.result_left = 0
        
        
        self.flip = False                       # Flip detected flag
        self.gap = False                        # Gap detected flag
        self.obs = False                        # Obstacle detected flag
    
        # Setup of GPIO pins of the Raspberry
        GPIO.setmode(GPIO.BCM)
        GPIO.setup(self.StepperEnable, GPIO.OUT)
        GPIO.setup(self.StepperLeftDIR, GPIO.OUT)
        GPIO.setup(self.StepperLeftSTEP, GPIO.OUT)
        GPIO.setup(self.StepperRightDIR, GPIO.OUT)
        GPIO.setup(self.StepperRightSTEP, GPIO.OUT)
        GPIO.setup(self.MODE, GPIO.OUT)
        RESOLUTION = {'Full': (0, 0, 0),
                    'Half': (1, 0, 0),
                    '1/4': (0, 1, 0),
                    '1/8': (1, 1, 0),
                    '1/16': (0, 0, 1),
                    '1/32': (1, 0, 1)}
        GPIO.output(self.MODE, RESOLUTION['1/4'])
        
        
    # must be run in a seperate Thread
    def LeftMotor(self):
        self.get_logger().info('Starting left Steppermotor')
        while True:
            # print("LEFT {}".format(self.speed_delay_left))
            if self.speed_delay_left < self.delay_limits[1] * 0.98: 
                GPIO.output(self.StepperLeftDIR, self.l_dir)
                GPIO.output(self.StepperLeftSTEP, GPIO.HIGH)
                sleep(self.speed_delay_left/4)
                GPIO.output(self.StepperLeftSTEP, GPIO.LOW)
                sleep(self.speed_delay_left)
                # print("Left {}".format(self.speed_delay_left))
        
    # must be run in a seperate Thread
    def RightMotor(self):
        self.get_logger().info('Starting right Steppermotor')
        while True:
            # print("RIGHT {}".format(self.speed_delay_right))
            if self.speed_delay_right < self.delay_limits[1] * 0.98: 
                GPIO.output(self.StepperRightDIR,  self.r_dir)
                GPIO.output(self.StepperRightSTEP, GPIO.HIGH)
                sleep(self.speed_delay_right/4)
                GPIO.output(self.StepperRightSTEP, GPIO.LOW)
                sleep(self.speed_delay_right)
                # print("Right {}".format(self.speed_delay_right))
            
    
    def controller_callback(self, msg : XboxInput):        
        if (self.startup_right * 0.95 != msg.vel_r or self.startup_left * 0.95 != msg.vel_l) and self.enable_steppers(msg.motor_state):
            if self.flip:
                print("FLIP!")
                self.startup_right -= self.right_wheel.compute(abs(5), self.startup_right)
                self.startup_left -= self.left_wheel.compute(abs(5), self.startup_left)
                self.r_dir = self.CW
                self.l_dir = self.CCW
                
            elif self.gap:
                print("GAP!")
                self.startup_right -= self.right_wheel.compute(abs(4), self.startup_right)
                self.startup_left -= self.left_wheel.compute(abs(4), self.startup_left)
                self.r_dir = self.CCW
                self.l_dir = self.CW
                
            elif self.obs:
                print("OBSTICAL!")
                self.startup_right -= self.right_wheel.compute(abs(4), self.startup_right)
                self.startup_left -= self.left_wheel.compute(abs(4), self.startup_left)
                self.r_dir = self.CCW
                self.l_dir = self.CW
                
            else:
                if  msg.vel_r > 0:
                    self.r_dir = self.CW
                    # print("FORWARD RIGHT")
                    
                elif msg.vel_r < 0:
                    self.r_dir = self.CCW
                    # print("BACKWARD RIGHT")
                    
                if msg.vel_l > 0:
                    self.l_dir = self.CCW
                    # print("FORWARD LEFT")
                    
                elif msg.vel_l < 0: 
                    self.l_dir = self.CW
                    # print("BACKWARD LEFT")
                
                if abs(msg.vel_r) >= 9.0:
                    self.startup_right -= self.right_wheel.compute(abs(msg.vel_r), self.startup_right)
                    self.startup_left -= self.left_wheel.compute(abs(msg.vel_r), self.startup_left)
                else:
                    self.startup_right -= self.right_wheel.compute(abs(msg.vel_r), self.startup_right)
                    self.startup_left -= self.left_wheel.compute(abs(msg.vel_l), self.startup_left)
              
                
            self.result_right = self.startup_right
            self.result_left = self.startup_left
            
            self.speed_delay_left = self.map(self.result_left, self.vel_limits[0], self.vel_limits[1], self.delay_limits[1], self.delay_limits[0])
            self.speed_delay_right = self.map(self.result_right, self.vel_limits[0], self.vel_limits[1], self.delay_limits[1], self.delay_limits[0])
            
        if self.print_flag > 10:
            print("Input (left, right): \t\t\t{0},\t{1}".format(msg.vel_l, msg.vel_r))
            print("PID right:\t{}".format(self.result_right)) 
            print("PID left:\t\t{}".format(self.result_left))
            print("Motorstate: \t\t\t\t\t\t\t\t\t\t{}".format(msg.motor_state))
            
            self.print_flag = 0
        
        elif self.print_flag <= 10:
            self.print_flag += 1


    def IMU(self, msg : IMUSensor):
        now = time.monotonic()
        if msg.gyro.x > 100:
            print("Tilting {}".format(msg.gyro.x))
            self.flip = True
            self.flipping_time = now
            
        elif now - self.flipping_time >= 0.5:
            # print("Tilting {}".format(msg.gyro.x))
            self.flip = False
            
                     
    def TOF(self, msg : TOFSensor):
        now = time.monotonic()
        if msg.dist_value > 250:
            print("Drop detected: {}".format(msg.dist_value))
            self.gap_time = now 
            self.gap = True
            
        elif msg.dist_value < 100 and msg.dist_value >= 0:
            print("Obstacle detected: {}".format(msg.dist_value))
            self.obs_time = now
            self.obs = True
            
        elif self.gap and now - self.gap_time >= 1:
            print("Done gap {}".format(msg.dist_value))
            self.gap = False
            
        elif self.obs and now - self.obs_time >= 1:
            print("Done obs {}".format(msg.dist_value))
            self.obs = False
            
            
    def map(self,value, leftMin, leftMax, rightMin, rightMax):
        # Figure out how 'wide' each range is
        leftSpan = leftMax - leftMin
        rightSpan = rightMax - rightMin

        # Convert the left range into a 0-1 range (float)
        valueScaled = float(value - leftMin) / float(leftSpan)

        # Convert the 0-1 range into a value in the right range.
        return rightMin + (valueScaled * rightSpan) 
        
        
    def enable_steppers(self, enable):
        if enable:
            GPIO.output(self.StepperEnable, GPIO.LOW)
            return True
        else:
            GPIO.output(self.StepperEnable, GPIO.HIGH)
            return False
    
            
def main(args=None):
    rclpy.init(args=args)

    try:
        # declare the node constructor
        stepperControl = stepperMotorDriver()
        
        # #enabling the lidar
        # LidarEnable = 18
        # GPIO.setup(LidarEnable, GPIO.OUT)
        # GPIO.output(LidarEnable, GPIO.HIGH)
        
        # start seperate threads for the stepper control and run them as daemons so it stops on ros exits
        right_motor = Thread(target=stepperControl.RightMotor, args=(), daemon=True)
        left_motor = Thread(target=stepperControl.LeftMotor, args=(), daemon=True)
       
        executor = MultiThreadedExecutor(num_threads=3)
        
        try:
            right_motor.start()
            left_motor.start()
            
            # pause the program execution, waits for a request to kill the node (ctrl+c)
            rclpy.spin(stepperControl, executor)
            
        finally:
            # #disabling the lidar
            # GPIO.output(LidarEnable, GPIO.LOW)
            stepperControl.destroy_node()

    finally:
        # shutdown the ROS communication
        rclpy.shutdown()
        
    
if __name__ == '__main__':
    main()

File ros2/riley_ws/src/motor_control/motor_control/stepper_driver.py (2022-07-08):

#!/usr/bin/env python3
from cmath import pi
from time import monotonic, sleep

import rclpy
import RPi.GPIO as GPIO
from rclpy.constants import S_TO_NS
from rclpy.node import Node
from riley_interfaces.msg import XboxInput

from motor_control.pid import PID

class stepperMotorDriver(Node):

    def __init__(self):
        super().__init__('xbox_controller_subscriber')
        self.get_logger().info('Creating a subscriber to xbox controller now')
        self.subscription = self.create_subscription(XboxInput, 'xbox_input', self.listener_callback, 10)
        
        
        self.accelerating = False
        self.call_counter = 0
        self.current_speed = 0.0
        
        # pin values
        self.StepperRightDIR = 6     # Direction of motor 1
        self.StepperRightSTEP = 5    # Step of motor 1
        self.StepperLeftDIR = 26     # Direction of motor 2
        self.StepperLeftSTEP = 16    # Step of motor 2
        self.MODE = (22, 23, 24)     # Microstep Resolution GPIO Pins

        # GPIO pinmode init 
        GPIO.setmode(GPIO.BCM)
        GPIO.setup(self.StepperLeftDIR, GPIO.OUT)
        GPIO.setup(self.StepperLeftSTEP, GPIO.OUT)
        GPIO.setup(self.StepperRightDIR, GPIO.OUT)
        GPIO.setup(self.StepperRightSTEP, GPIO.OUT)
        GPIO.setup(self.MODE, GPIO.OUT)

        # stepper driver mode select
        self.RESOLUTION = {'Full': (0, 0, 0),
                    'Half': (1, 0, 0),
                    '1/4': (0, 1, 0),
                    '1/8': (1, 1, 0),
                    '1/16': (0, 0, 1),
                    '1/32': (1, 0, 1)}
        self.used_resolution = '1/4'
        GPIO.output(self.MODE, self.RESOLUTION[self.used_resolution])

        # Declarations
        if   self.used_resolution == 'Full': self.SPR = 2 * pi / (1.8 * pi/180)             # Steps per Revolution (200)
        elif self.used_resolution == 'Half': self.SPR = 2 * pi / (1.8 * pi/180) / (1/2)     # Steps per Revolution (400)
        elif self.used_resolution == '1/4':  self.SPR = 2 * pi / (1.8 * pi/180) / (1/4)     # Steps per Revolution (800)
        elif self.used_resolution == '1/8':  self.SPR = 2 * pi / (1.8 * pi/180) / (1/8)     # Steps per Revolution (1600)
        elif self.used_resolution == '1/16': self.SPR = 2 * pi / (1.8 * pi/180) / (1/16)    # Steps per Revolution (3200)
        elif self.used_resolution == '1/32': self.SPR = 2 * pi / (1.8 * pi/180) / (1/32)    # Steps per Revolution (6400)
        # print("Steps per revolution: {}".format(SPR))
        self.RFW = False      # Clockwise Rotation
        self.LFW = True     # Counterclockwise Rotation

        # Variables
        self.step_count = 0
        self.last_step_count = 0
        self.last_time = monotonic()                     # current time
        self.delay_limits = (0.002, 0.2)
        self.vel_limits = (0.0, 10.0)                    # 
        self.vel = 0.0                                   # 
        self.desired_speed = 0.0                         # 
        self.result = 0
        self.wheel_diameter = 0.1263365                  # in m
        self.wheel_radius = self.wheel_diameter / 2      # in m
        # print("Wheel radius: {}".format(wheel_radius))

        self.angle_of_step = 2 * pi / self.SPR                # in radian
        # print("Angle of a step: {}".format(angle_of_step))

        self.distance_of_step = self.wheel_radius * self.angle_of_step     # calc distance per step
        # print("Distance of a step: {}".format(distance_of_step))

        self.right_wheel = PID(kp=0.03, direction=1, output_limits=self.vel_limits, updateTime=0.005)
        # left_wheel = PID(output_limits=vel_limits, updateTime=0.001)
        
        self.timer = self.create_timer(self.result, self.MoveForward)
        self.timer.cancel()
        

    def listener_callback(self, msg : XboxInput):
        self.call_counter += 1
        
        if msg.vel_r >= 1:
            if desired_speed != msg.vel_r:
                self.get_logger().info("Forward motion triggered")
                desired_speed = msg.vel_r
                self.accelerating = True

        elif msg.vel_r <= 1:
            if desired_speed != msg.vel_r:
                self.get_logger().info("Stop motion triggered")
                desired_speed = self.vel_limits[0]
                self.accelarating = False
        
        else:
            desired_speed = self.vel_limits[0]
        
        
        if self.accelerating:
            # control speed
            # vel = right_wheel.compute(desired_speed, self.getCurrentSpeed())
            vel = self.right_wheel.compute(desired_speed, self.current_speed)
            self.current_speed += vel
            self.get_logger().info("New velocity: {}".format(self.current_speed))
            # left_wheel.compute(vel_limits[1], current)
            
            #                       low             high          high             low
            result = self.map(self.current_speed, self.vel_limits[0], self.vel_limits[1], self.delay_limits[1], self.delay_limits[0])
            # print("Result = {}".format(result))
        else:
            vel = 0
            self.current_speed += vel
            #                       low             high          high             low
            result = self.map(self.current_speed, self.vel_limits[0], self.vel_limits[1], self.delay_limits[1], self.delay_limits[0])
            # print("Result = {}".format(result))
        
        if result == self.delay_limits[1]:
            result = 0
            self.timer.cancel()
        else:
            self.timer.reset()
            self.get_logger().info("Resulting delay = {}".format(result))
            self.get_logger().info("Changing time now")
            self.timer.timer_period_ns = result * S_TO_NS
    
    # Mapper, fucking always works
    def map(self, value, leftMin, leftMax, rightMin, rightMax):
        # Figure out how 'wide' each range is
        leftSpan = leftMax - leftMin
        rightSpan = rightMax - rightMin

        # Convert the left range into a 0-1 range (float)
        valueScaled = float(value - leftMin) / float(leftSpan)

        # Convert the 0-1 range into a value in the right range.
        return rightMin + (valueScaled * rightSpan)
            
    def getDistance(self):    
        global last_step_count
        # calc step difference
        step_difference = step_count - last_step_count
        self.get_logger().debug("Step difference: {}".format(step_difference))
        
        # calc distance
        distance = self.distance_of_step * step_difference
        self.get_logger().debug("Distance: {}".format(distance))
        
        # save steps
        last_step_count = step_count
        # return distance
        return distance
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

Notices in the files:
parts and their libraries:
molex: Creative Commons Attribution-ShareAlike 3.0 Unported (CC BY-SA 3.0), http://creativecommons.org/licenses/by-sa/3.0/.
